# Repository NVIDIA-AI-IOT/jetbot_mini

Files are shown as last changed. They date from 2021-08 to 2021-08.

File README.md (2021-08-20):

# Jetbot Mini

<p align="left">
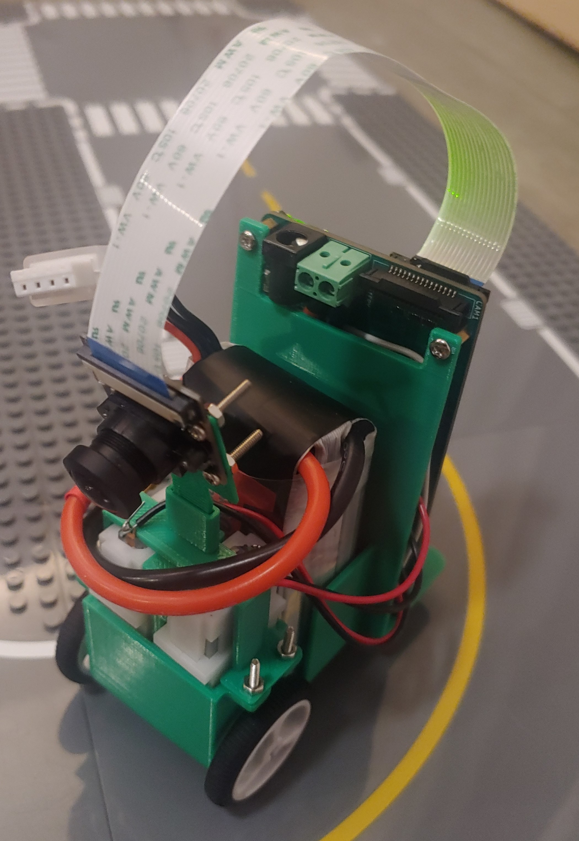
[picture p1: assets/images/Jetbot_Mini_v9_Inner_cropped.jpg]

</p>

This is the Jetbot Mini project, a smaller iteration of the [Jetbot](https://github.com/NVIDIA-AI-IOT/jetbot)! Some key features are as follows:
* Onboard motor controller and battery charger to reduce costs and wire clutter
* Custom baseboard for the Jetson Nano module
* A smaller chassis that can achieve two way traffic (i.e., two robots running on the road at the same time) on the LEGO roads used to test the original Jetbot
* Designed with KiCAD and Onshape for easy maker access

This project aims to be an accessible example project that uses the Jetson Nano platform and a custom baseboard, so any feedback about the design is welcome. 

**Please note that the A00 Baseboard design is not recommended for manufacture, as it requires a rework to work properly and some features have not been fully validated. The A01 Baseboard is currently in development that aims to fix issues found with A00.**

https://user-images.githubusercontent.com/46247601/129587346-760dd624-837d-4d27-9475-d30973f9e246.mp4

## Get Started and Involved!

Refer to [this](https://github.com/NVIDIA-AI-IOT/jetbot_mini/blob/main/docs/getting_started_with_A00.md) document to get a sense of how to use this repository and learn from this project!
This project is intended as a learning tool for makers, and any feedback related to the project is greatly appreciated!
* Report a bug by [creating an issue](https://github.com/NVIDIA-AI-IOT/jetbot_mini/issues)

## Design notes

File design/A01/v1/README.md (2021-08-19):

# Setup

While developing the schematic and layout designs, I used some footprints from SnapEDA; in order to avoid dealing with licensing issues, I will not redistribute those files on this Github and instead link to where you can download the necessary files. 

## Symbol Library Setup

To get setup for the schematic, download the files and import the libraries "Jetbot Mini-rescue" and "Jetbot_Mini_Symbols" in the "libs" folder. 

In order to import a library, go through the following steps:
1. Download the .dcm and .lib files and remember where you stored them on your computer
2. Download the rest of the KiCAD files and open up the .pro file
3. Go to Preferences --> Manage Symbol Libraries --> Project Specific Libraries --> Add Existing Library to Table (folder icon on lower left of dialogue box)
4. Navigate to where the .lib files are stored on your computer and select the files
5. The libraries should be imported and when you try to add a component to the schematic, you should see the libraries show up

You may need the download the following symbol libraries from the KiCAD github: https://github.com/KiCad/kicad-symbols

| Library Name |
| :--- |
| Connector |
| Connector_Generic |
| Logic_LevelTranslator |

## Footprint Library Setup

To get setup for the layout design, you need the following SnapEDA footprint files (you need to make an account if you don't have one already, download the footprint and unzip the package):

| MPN | Device | Reference(s) | Link |
| :--- | :--- | :--- | :--- |
| 692121130100 | USB3 Type A | J8 | https://www.snapeda.com/parts/692121130100/Wurth%20Elektronik/view-part/4900658/?ref=search&t=692121130100 |
| 2309411-5 | DDR4 SODIMM Connector | J1 | https://www.snapeda.com/parts/2309411-5/TE%20Connectivity/view-part/2404627/?ref=search&t=2309411-5 |
| TPD1E05U06DPYR | ESD Diodes | D1, D9 | https://www.snapeda.com/parts/TPD1E05U06DPYR/Texas%20Instruments/view-part/383548/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 |
| BG300-04-A-L-A | Motor Header | J4 | https://www.snapeda.com/parts/BG300-04-A-L-A/Global%20Connector%20Technology/view-part/696206/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 |
| LQH44PN100MP0L | 3V3 Buck Converter Inductor | L1 | https://www.snapeda.com/parts/LQH44PN100MP0L/Murata/view-part/?ref=dk&t=IND_LQH44PN100MP0L&con_ref=None |
| 1935161 | Battery Screw Terminal | J12 | https://www.snapeda.com/parts/1935161/Phoenix%20Contact/view-part/423515/?ref=search&t=1935161 |
| AP6503 | 3V3 Buck Converter | U17 | https://www.snapeda.com/parts/AP6503SP-13/Diodes%20Inc./view-part/562785/?ref=search&t=AP6503 |
| TPD4E05U06DQAR | ESD Diodes | U1, U2, U5, U7, U9, U20, U25, U28 | https://www.snapeda.com/parts/TPD4E05U06DQAR/Texas%20Instruments/view-part/431231/?ref=search&t=TPD4E05U06DQAR |
| 1N4148WT | Diode | D10 | https://www.snapeda.com/parts/1N4148WT/ON%20Semiconductor/view-part/2771069/?ref=search&t=1N4148WT |
| AT24C02D-MAHM-T | EEPROM | U22 | https://www.snapeda.com/parts/AT24C02D-MAHM-T/Microchip/view-part/229652/?ref=search&t=AT24C02D-MAHM-T |
| 74LVC4245A | Level Shifter | U23 | https://www.snapeda.com/parts/74LVC4245APW/Nexperia%20USA/view-part/557968/?ref=search&t=74LVC4245A%20 |
| 74LVC1G126W5-7, 74LVC1G07W5-7 | Tri-State Buffer | U11, U12, U14, U31 | https://www.snapeda.com/parts/74LVC1G126W5-7/Diodes%20Inc./view-part/234182/?ref=search&t=74LVC1G126W5-7 |
| B3SL-1022P | Push Button | SW1 | https://www.snapeda.com/parts/B3SL-1022P/Omron/view-part/215208/?ref=search&t=B3SL-1022P |
| 1-1734248-5 | Camera Connectors | J2, J3 | https://www.snapeda.com/parts/1-1734248-5/TE%20Connectivity/view-part/?ref=te_in&t=1-1734248-5&con_ref=None |
| B340A-13-F | Schottky Diode | D5, D8 | https://www.snapeda.com/parts/B340A-13-F/Diodes%20Inc./view-part/78704/?ref=search&t=B340A-13_F |
| LQH44PN100MP0L | 10uH Inductor for 3V3 Buck | L1 | https://www.snapeda.com/parts/LQH44PN100MP0L/Murata/view-part/4547005/?ref=search&t=LQH44PN100MP |

In order to import the footprints, go through the following steps:
1. Download the KiCAD files to your computer
2. Open the .pro file and click "Footprint Editor" on the top ribbon, the icon is a 6 pin package with green pins
3. Go to File --> New Library --> Create library with name of your choice (should have .pretty extension) in place of your choice, it is typical to keep everything with the KiCAD files --> Choose local
4. Your library should be created, then add the .kicad_mod files from the downloaded SnapEDA folders to the .pretty folder
5. Open up the schematic and go to "Assign PCB footprints to schematic symbols" on the top ribbon, and assign the footprints from your custom library to each of the corresponding symbols

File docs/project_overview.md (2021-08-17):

# Project Overview

<p align="left">

</p>

The [Jetbot](https://github.com/NVIDIA-AI-IOT/jetbot) is a self-driving robot that harnesses neural networks, a camera, motors, and the Jetson Nano module to do cool things like follow roads and avoid obstacles. It is a fantastic learning tool for hobbyists, students and makers to get familiar with neural networks and AI. 

This project, the Jetbot Mini, is meant as a smaller iteration of the [Jetbot](https://github.com/NVIDIA-AI-IOT/jetbot) with a new custom baseboard with an integrated motor controller and battery charger to reduce cost and wire clutter when assembling. The main design goal was to achieve two-way traffic on the LEGO roads used to test the original Jetbot; this goal is meant to facilitate a cool demo and prove how custom baseboards can result in optimizations for these kinds of projects. 

<p align="left">
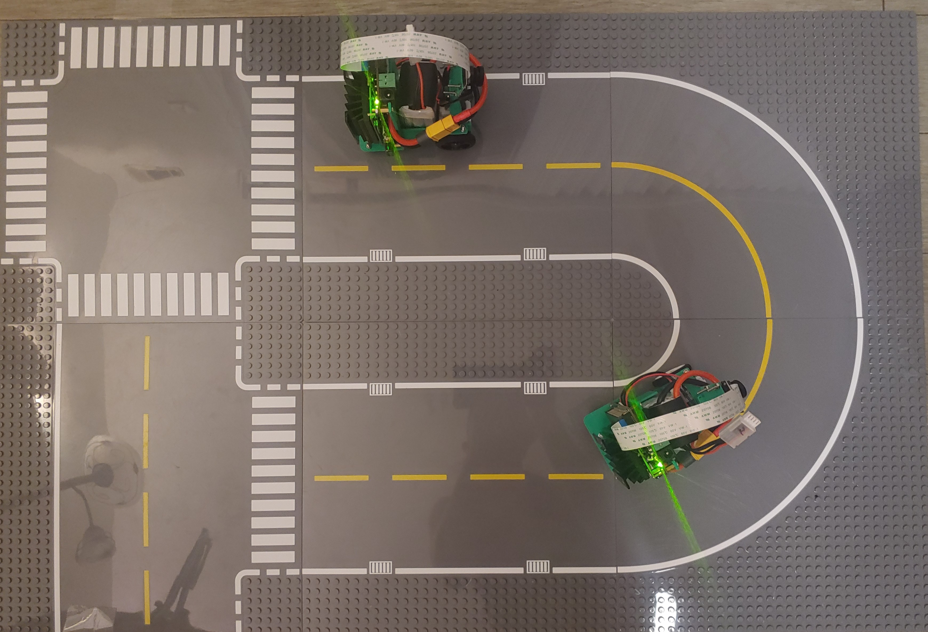
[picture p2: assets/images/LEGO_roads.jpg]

</p>

The overall goal and ethos of this project is to make all the design files open source and provide an example of custom hardware for the Jetson Nano module that makers, students, and hobbyists can learn from and either improve the design, or use it to help them create their own custom hardware. You are encouraged to download the design files and play around with them! 

> As mentioned in the overall README, the A00 baseboard is not recommended for manufacture as the boards have not been fully validated and require an extensive rework to work properly. A01, the next iteration of the schematic, is currently being worked on. 

Another design goal was to make the Jetbot Mini cheaper to manufacture, although that is currently being worked. More information can be found in the bill_of_materials.md file. 

## Feature Set

The following table shows the feature set comparison between the B01 Developer Kit for the Jetson Nano, which was used for the original Jetbot, and the A00 baseboard, used for Jetbot Mini. 

| Features | B01 Developer Kit | A00 Baseboard |
| :--- | :--- | :--- |
| USB | 4x USB 3.0, 1x USB 2.0 Micro-B | 1x USB 3.0, 1x USB 2.0 Micro-B |
| Display | HDMI and DP | None |
| Camera | 2x MIPI CSI-2 DPHY Lanes | 2x MIPI CSI-2 DPHY Lanes |
| Connectivity | Gigabit Ethernet, M.2 Key E | Wifi via USB Dongle |
| Other | GPIO, I2C, I2S, SPI, UART | I2C, UART, Battery Management System, Motor Controller|

Note that a lot of the features from the B01 Dev Kit were cut, and this was done to facilitate a smaller baseboard and thus a smaller overall chassis to hit the two-way LEGO road traffic specification. The following is an IO block diagram showing all the IO on the board:

<p align="left">
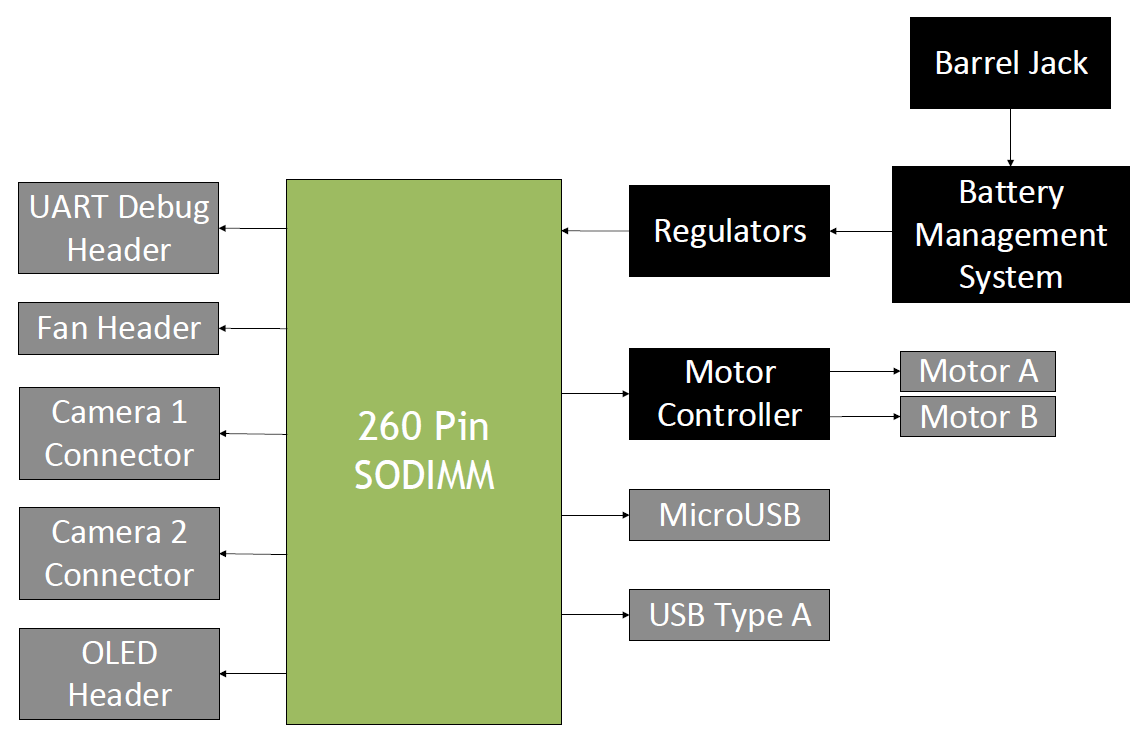
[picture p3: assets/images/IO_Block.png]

</p>

The following table shows what each feature is used for:

| Feature | Justification | 
| :--- | :--- |
| 1x USB 3.0 Type A | Used for Wifi Connectivity to control the robot. Using a wired connection like ethernet is not practical for a moving robot, and eliminating the need for M.2 reduces wire clutter within the robot and cost | 
| 1x USB 2.0 Micro-B | Used for a headless connection to set up the Jetson Nano and for debugging in recovery mode |
| 2x Camera Connectors | Used for vision and movement, and the option for a second camera allows the user flexibility if they want to add an additional camera for more optimized movement |
| OLED Header | Connects over I2C to the Jetson Nano module, and displays the IP address to connect to |
| Fan Header | Four pin connector with tach and PWM used to control an optional fan; note that the Jetbot Mini does not use a fan to reduce chassis footprint | 
| UART Debug Header | Six pin connector compatible with the FTDI friend for debugging and for terminal access | 
| Battery Management System | Eliminates the need for a seprate batter charger and the user does not have to take the Jetbot Mini apart if they wish to charge the battery | 
| Motor Controller | Eliminates the need for a separate motor controller / driver module, which notably the Jetbot requires; this reduces wire clutter and cost |
| EEPROM | Used to store information about the baseboard and used by software; differences in iterations like GPIO might need different software, so this is to help with identification |

A more in-depth dive in to the different features and board design is available in docs/board_design/A00/!

Below shows a comparison between the B01 Dev Kit (Left) and the A00 Baseboard (Right), note how cutting all that IO saved a lot of space!

<p align="left">
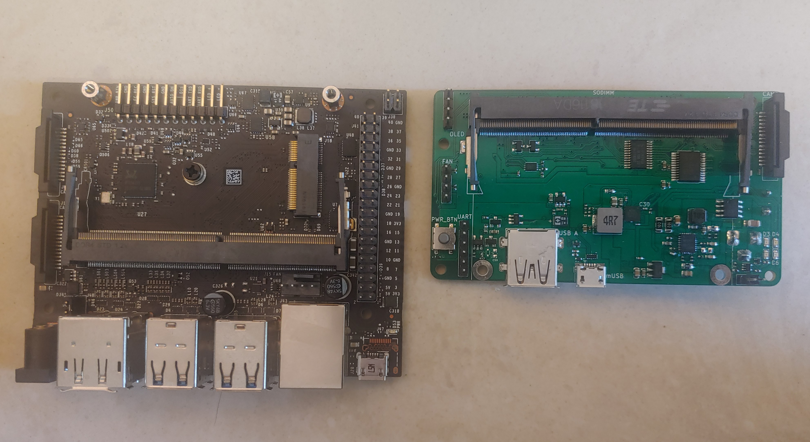
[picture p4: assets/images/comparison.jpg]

</p>

## Design Environment

KiCAD was the tool of choice for schematic and layout design, as it is a free and open-source software widely available for makers. Onshape was used to design the CAD files, and was chosen as it is a cloud-based and easy to use software that is a popular choice among makers. 

## Design Process

The general flow for this project is the following:

Project Conception and Design Goal Specifications --> Schematic + Symbol Design --> BOM Development --> Footprint Design --> Layout --> Design Review --> Gerber Out (means send gerber files to manufacturing house and get design manufactured) --> Bring-Up (Basic power rails and IO check, debug anything not working) and Validate (extensively check each signal, make sure voltage, current and circuit behavior are as expected, check for longevity) Boards --> Chassis Design --> Chassis Prototyping --> Software Integration --> Testing and Acquiring Demo

**And throughout this process, always document every choice thoroughly!!!**

Specifics of the choices for batteries, schematic and layout design, and chassis design are found in their respective folders. 

## Future Work

A01 is still in development but will eventually be gerbered out and validated. In the meantime any Work-In-Progress bugs, features, and edits can be found in the [Issues](https://github.com/NVIDIA-AI-IOT/jetbot_mini/issues) tab of this repository; feel free to create issues, provide feedback and comment on the project!

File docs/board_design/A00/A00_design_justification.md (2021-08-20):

# Design Justification for A00 Schematic and Layout Design

In this document, I will try to explain the justification for every design choice made. First, some basic things:

* I initially chose BOM components from Seeed Studio's libraries, as I thought that I would be getting the boards manufacturing from them. However, during the summer of 2020, the cost of the boards turned out to over a thousand dollars, and we decided to switch to PCBway, who were cheaper and had a more extensive library. 
* Most of the schematic design was referenced from either the B01 Developer Kit (design files can be found [here](https://developer.nvidia.com/embedded/downloads)) or the datasheets of the ICs and components used, and the Jetson Nano datasheet, product design guide, and developer kit user guide were used references extensively (these files can also be found [here](https://developer.nvidia.com/embedded/downloads)).

## Power Tree

After deciding on the initial feature set for the Jetbot Mini, a power tree was drawn up to decide on the power rails and determine the input and output requirements for each rail based on the components on the rails. This data then can be used to choose the buck converter and battery specifications. Data was also taken for the power drawn (in mW) by the Jetson Nano module during various operation modes to factor into the power trees. The [Waveshare Jetbot kit](https://www.waveshare.com/catalog/product/view/id/3756) was used for this testing. The rest of the power consumption data for the different components were referenced from the respective datasheets. Two power trees were drawn up, one with estimated values, and one adjusted for buck converters chosen; the main difference is the efficiency was changed from an assumption to an actual value. The power trees can be found [here](https://github.com/NVIDIA-AI-IOT/jetbot_mini/tree/main/docs/board_design/A00/power_tree).

The power rails are summarized below:

| Power Rail | Power Component Used | Power Component Max Output Current | Max Output Current (from Power Tree) | Components on Power Rail |
| :--- | :--- | :--- | :--- | :--- |
| 5V | GS9238 | 8 A | 4.48 A | Jetson Nano module, motors, OLED, Power Logic, Fan, USB3 Type-A, Motor Driver, Level Shifters |
| 5V_AO | AS78L05 | 100 mA | ~0.0000204 A | Power Logic |
| 3V3 | AP6503 | 3 A | 0.52 A | Cameras, Motor Driver, Level Shifters, Camera Mux |
| 1V8 | TLV70218DBVR | 300 mA | ~0.000049 A | Level Shifters |

## Battery Choice

The battery needed to be small, inexpensive, and be able to ideally power the Jetbot Mini for 1 hour. After creating the power tree, typical current draw from the battery was determined to be around 1.235 A at 12 V, and so a 1500 mAh battery was pursued. The most viable and readily available option was an RC LiPo battery; note that the eventual battery charger chosen is technically a Li-Ion battery charger, but the two battery chemistries have a similar charging curve and I received approval to use it for LiPo batteries. The following table shows some of the options considered at the time:

| Battery Name / Manufacturer | Battery Type | Capacity | C Rating | Size (L x W x H, in) | Connector Type | Price Per Battery | Comments | Links |
| :--- | :--- | :--- | :--- | :--- | :--- | :--- | :--- | :--- |
| INIU Power Bank | 5V / 3A High-Speed 2 USB ports | 10000 mAh | N/A | 5.1 x 2.7 x 0.6 | USB | $19.99 | Used on Original Jetbot | [Amazon](https://www.amazon.com/gp/product/B07H6LB4J4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) |
| Tattu | 3S LiPo | 1300 mAh | 45 C | 2.83 x 1.44 x 0.89 | XT60 | $15.99 | Cheap and small, but low capacity | [Amazon](https://www.amazon.com/Tattu-Battery-1300mAh-11-1V-Airplane/dp/B013I9RLVK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) |
| HOOVO | 3S LiPo | 1500 mAh | 120 C | 2.68 x 1.36 x 1.08 | XT60 | $15.50 | High discharge rate! 2 Pack. | [Amazon](https://www.amazon.com/HOOVO-Quadcopter-Helicopter-Airplane-Multi-Motor/dp/B07W1PFWB6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) |
| GOLDBAT | 3S LiPo| 1500 mAh | 100 C | 2.83 x 1.38 x 1 | XT60 | $13.99 | 2 Pack. High discharge rate, relatively low capacity. | [Amazon](https://www.amazon.com/GOLDBAT-Softcase-m4-fpv250-Shredder-Helicopter/dp/B07ZFDJWR1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) |
| Youme Power | 2S LiPo | 5200 mAh | 50 C | 5.31 x 1.65 x 0.83 | Deans T Plug | $17.99 | 2 Pack. Seems to be a bit large for a 2S battery | [Amazon](https://www.amazon.com/Battery-5200mAh-Helicopter-Airplane-Racing/dp/B07LGSCPFG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) | 
| Ovonic | 2S LiPo | 5200 mAh | 50 C | 5.39 x 1.81 x 0.94 | Deans T Plug | $15.50 | 2 Pack. | [Amazon](https://www.amazon.com/OVONIC-Batteries-Dean-Style-Connector-Associated/dp/B07CVBQW5T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) |  
| Tattu | 2S LiPo | 450 mAh | 75 C | 2.40 x 0.63 x 0.59 | XT30 Plug | $8.46 | 4 pack. Smallest battery so far! But also smallest capacity. | [Amazon](https://www.amazon.com/Tattu-Packs-450mAh-7-4V-Battery/dp/B07K18DJG5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) |

I decided to go with the GOLDBAT because it was the smallest and cheapest battery available while hitting the hour long specification. 

Some additional notes about batteries and battery chargers:
* The C-rate specifies the speed a battery is charged or discharged. For example, a 1000 mAh battery discharged at 1 C should be able to maintain 1 A for 1 hour, and if it is discharged at 2 C, it should maintain 2A for 30 minutes. RC batteries in particular need to deliver huge amounts of current, and thus have high C ratings; however, this feature is not necessary for this project. 
* NTC (negative temperature coefficient): resistance of the material decreases with temperature.
* Constant Current: Vary the voltage to maintain a constant current flow, switching off when the voltage reaches the level of a full charge. The design is usually used for NiCd and NiMH cells or batteries
* Constant Voltage: "allows the full current of the charger to flow into the battery until the power supply reaches its pre-set voltage.  The current will then taper down to a minimum value once that voltage level is reached."

References: https://www.heliosps.com/knowledgebase/battery-charging-methods-terminology/ and Battery University. 

## Schematic Design

In general:
* 0 ohm resistors are used throughout the design for testing purposes; they can be used as points to attach probe wires and inject noise.
* You will often see capacitors on the input rails to ICs and power supplies; these capacitors are there to help deal with noise, stabilize the power supply and voltage ripple, and help with sudden current requirements. The impedance of a capacitor is dictated by 1/jwC, where w is 2 x pi x frequency and C is the capacitance; at high frequencies, the impedance of a capacitor is near zero, which means the component is essentially a short to ground. This means high frequency noise is shunted to ground instead of entering the IC. Also, the capacitors act as small voltage reservoirs, and thus if the input voltage dips below the stored voltage, the capacitor can briefly supply power to the IC. In addition, the smaller 0.1uF capacitors are to help if the IC needs to pull a sharp current suddenly, perhaps due to a change in load. Larger capacitors will have ESR (equivalent series resistance) and ESL (equivalent series inductance) which will fight against that current pull, but smaller capacitors have smaller parasitics that help facilitate large current draw. These small 0.1uF capacitors do not store that much power, but will help with the sudden rising and falling edges for things like digital circuits. 
* The following [forum page](https://forum.digikey.com/t/calculating-capacitor-esr-from-tan/2633) is useful for calculating MLCC parasitic values. MLCC ESR and ESL values are also often listed on the manufacturer website in the form of graphs.

### Page 2 of A00 Schematic: Camera

<p align="left">
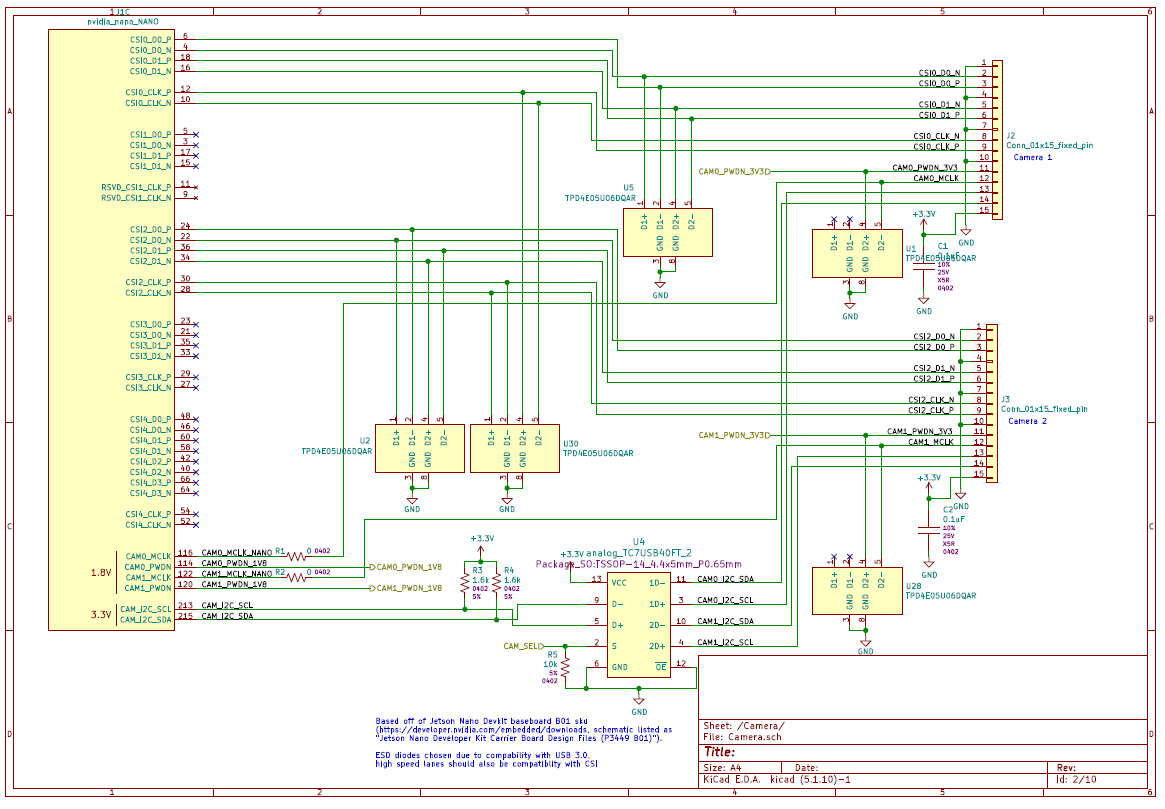
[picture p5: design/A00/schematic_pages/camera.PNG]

</p>

* Most of the camera connector (J2 and J3) connections were referenced from the B01 Developer Kit files. 
* No ESD on the CAM0_I2C_SDA, CAM0_I2C_SCL, CAM1_I2C_SDA, and CAM1_I2C_SCL lanes, as the TC7USB40FT has ESD on the output lines.
* TPD4E05U06DQAR ESD diodes chosen due to availability in target manufacturer libraries and because they are compatible with USB 3.0; using these diodes for the CSI lanes eliminates the need for separate ESD diodes. They have 0.5pF capacitance. Datasheet states compatibility with high speed signals. 
* CAM0 and CAM1 PWDN signals are level shifted from 1V8 to 3V3 for compatibility with new higher quality raspberry pi cameras; note that the B01 Developer Kit is not compatible with these cameras. 
* U4 is a mux used to switch between camera 1 and camera 2. 
* Note that when the Jetson Nano module boots up, it pings the camera I2C lanes to see if a camera module is attached and employs a startup sequence with PWDN; if no camera module is detected, calling camera commands will not send any data to the camera lanes. 
* Note that only a 0.1 uF capacitor is needed on the power rail of the camera connector, as the parasitics from the ribbon cable that connects the camera module to the camera connector prevents the camera board from seeing the additional capacitors effectively. The current spikes that the capacitors are meant to deal with are negated by the inductance of the camera ribbon cable.
* R5 is a pull-down resistor for the camera select pin of the mux, so that the default setting for the mux is lane 1. 

### Page 3 of A00 Schematic: Motors

<p align="left">
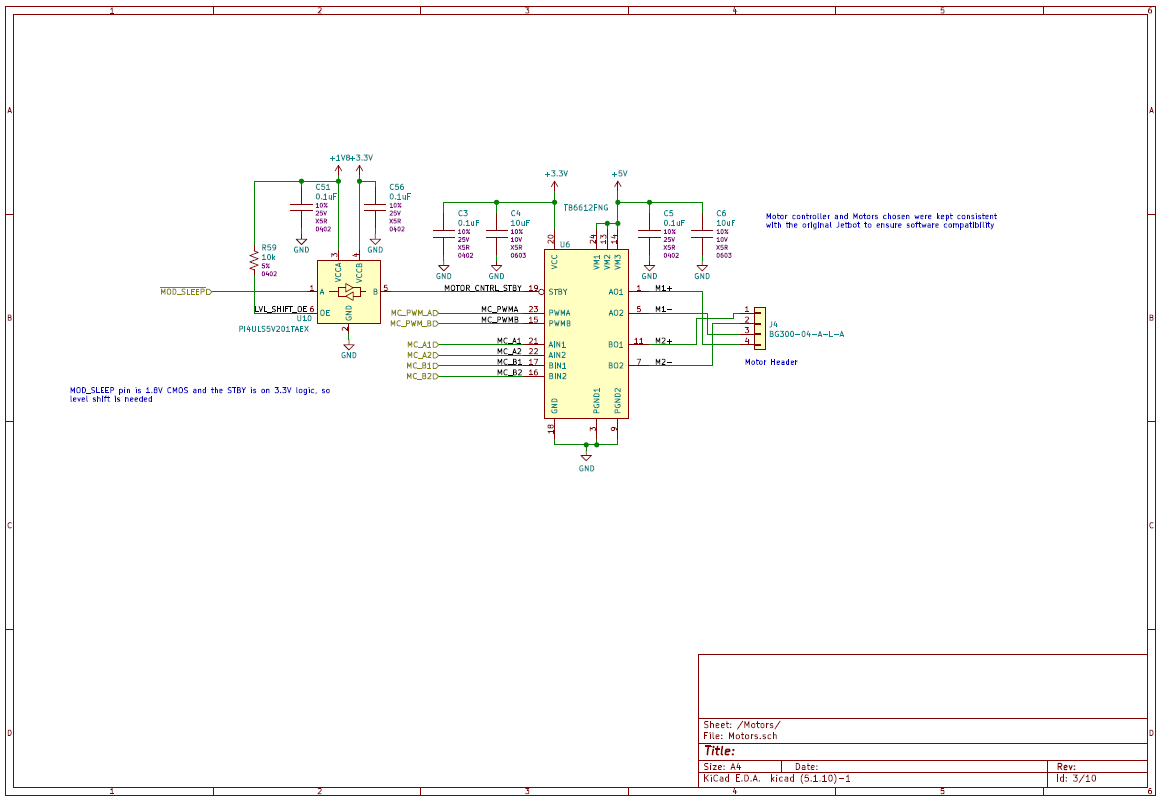
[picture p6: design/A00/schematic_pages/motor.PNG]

</p>

* The same motor controller IC as the Jetbot, the TB6612FNG, was used to ensure compatibility with Jetbot software. Note that the A00 baseboard uses GPIO instead of I2C to control the motors.
* Motor speed is controlled via PWMA and PWMB. 
* Motor A direction is controlled by AIN1 and AIN2, and motor B direction is controlled by BIN1 and BIN2. If both pins are off or on, the motor is turned off. See TB6612FNG datasheet or tutorial for exact directions based on pins. 
* Capacitor values on power rails were suggested by datasheets, and voltage ratings are high because those capacitor values are used elsewhere on higher voltage lines; using the same capacitor saves cost by eliminating the need for a unique part on the BOM. 
* The MOD_SLEEP pin that controls standby for the motor controller (i.e., tells the motor controller to turn off for a bit and conserve power) is on 1V8 logic, and the STBY pin is on 3V3 logic, so the level shifter is needed to translate between the two voltage levels. 
* Motor header is surface mount and placed underneath the board, as initially I thought that the chassis design would put the motors underneath the board, and so it would be easier to connect if the headers were on the bottom of the board. The Jetbot Mini test chassis ended up mounting the baseboard vertically, but it still worked out OK as the motors were in front of the motor headers.
* Note that different motors were used than the Jetbot to facilitate a smaller chassis design; the motors chosen ended up having a lower stall current than the TT motors used for the Jetbot, and thus would mean less strain on the 5V Buck Converter. 
* R59 pulls output enable high to enable the level shifter.

### Page 4 of A00 Schematic: USB

<p align="left">
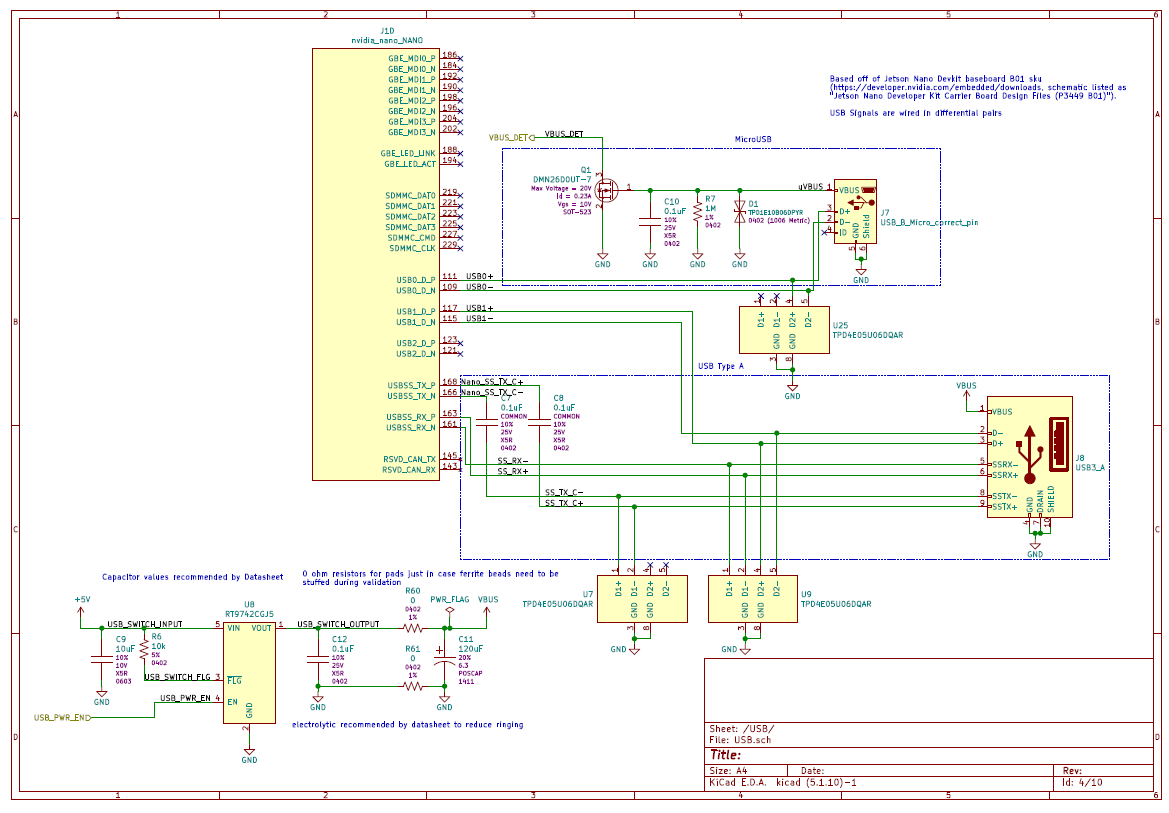
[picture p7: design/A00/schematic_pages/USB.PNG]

</p>

* This part of the circuit was heavily referenced from the B01 Developer Kit schematic.
* TPD4E05U06DQAR ESD diodes were chosen due to their compatibility  with USB devices and should be placed as close as possible to the connector on the layout.
* microUSB: J7
  * D1 to protect against ESD strikes when user pulls microUSB head in and out of the connector. 
  * R7 pulls the gate of Q1 initially low, and when a microUSB is connected VBUS_DET is connected to ground and lets the Nano module know that something is connected.
* USB3 Type-A: J8
  * C7 and C8 are AC-coupling capacitors and should be placed as close as possible to the transmission source on the layout. AC-coupling capacitors block DC bias. 
  * The USB switch U8 is needed to protect the host, as the USB might be drawing too much current, and also allows for power cycling the USB. The chosen part hits the required spec of max current draw for USB3 Type-A being 0.9 A. 
  * Capacitor values chosen based off the datasheet. 0 ohm resistors there just in case ferrite beads need to be stuffed during validation or if found that they are necessary.
  * C11 was switched from electrolytic to POSCAP to reduce the footprint size. 

### Page 5 of A00 Schematic: Fan

<p align="left">
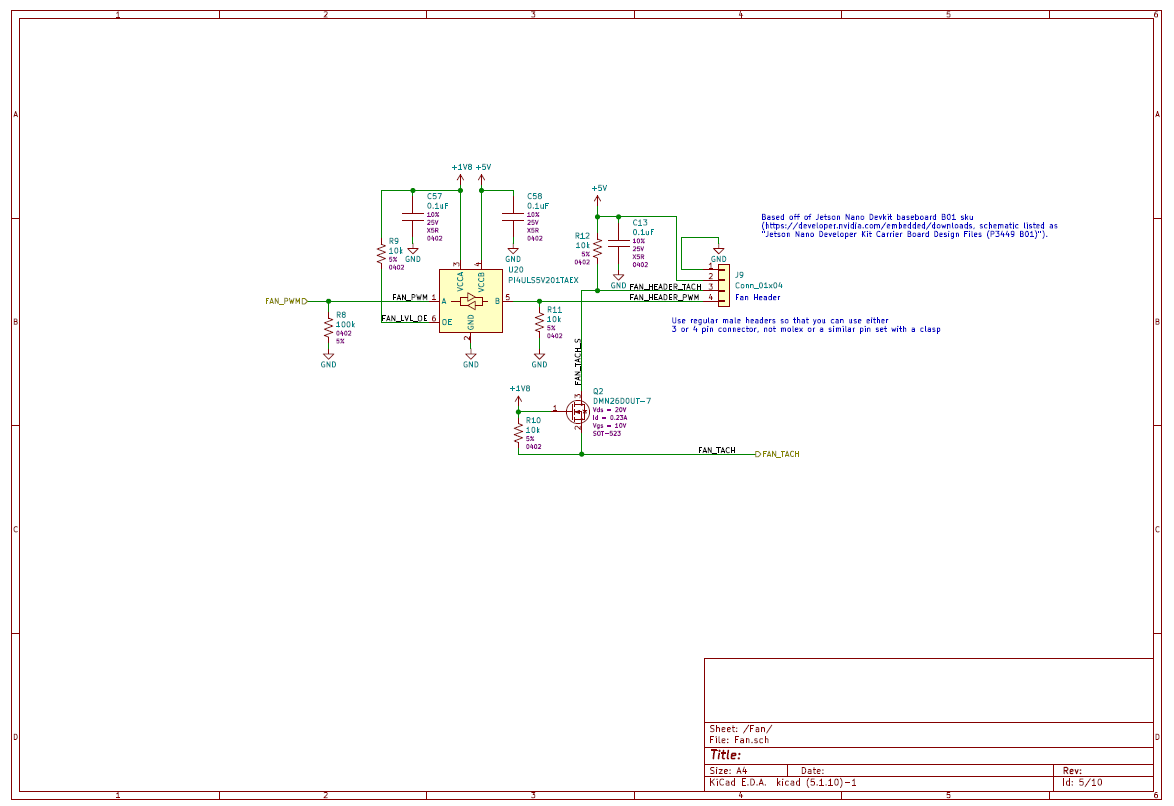
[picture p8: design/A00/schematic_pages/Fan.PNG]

</p>

* PWM level shifted to 5V to work properly with fan. 
* C13 is a decoupling capacitor for power rail of the fan. 
* PWM signals pulled low via R8 and R11, so initial state of PWM is zero.
* The Tach signal uses a level shifter (that should only be used with open drain signals!) that works as follows: the FAN_HEADER_TACH signal will output a square wave that drives low and has an open drain high that is pulled to 5V via R12. When the signal is driven low, the drain of Q3 is drive low. Before this time, Q2 was off as the gate and source are connected to 1V8, meaning Vgs = 0 < Vgsth; however, when the drain of Q2 is driven low, the body diode is in forward bias and thus connects source to zero. The current path from 1V8 to 0 has R10 in the way, so current is not too high. Q2 is turned on, and the FAN_TACH sees a logic low. When FAN_HEADER_TACH is driven high to 5V, the body diode is in reverse bias, which disconnects the source from the drain and turns off Q2. In this state, FAN_TACH sees 1V8, or a logic high. Thus, FAN_TACH sees a square wave ranging from 0 to 1V8, whose frequency is proportional to the fan speed. 

### Page 6 of A00 Schematic: Power_1

<p align="left">
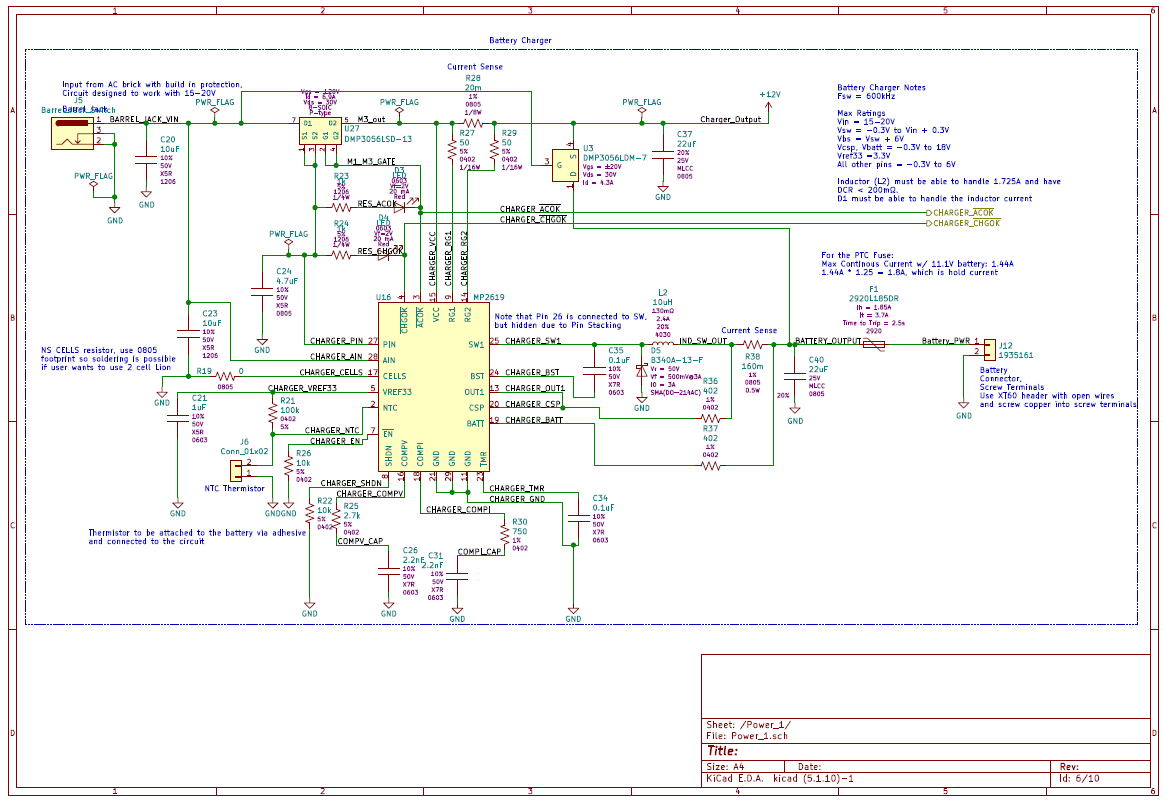
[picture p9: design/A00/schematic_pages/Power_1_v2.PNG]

</p>

* This is the battery charger circuit, with the battery charger IC of choice being MP2619 due to its low cost, availability and my team's experience with it. 
* Most of this circuit was referenced from the MP2619 datasheet example circuit. 
* Some noteworthy features / things to keep in mind:
 * This charger circuit DOES NOT feature charge balancing, so this will effect the longevity of your batteries. 
 * An NTC thermistor is required for charging to occur. If the thermistor becomes too hot or cold, charging will stop. 
 * DMP3056LSD-13 and DMP3056LDM-7 chosen with Vds that can handle at least 30V, as the highest voltage the battery charger can take is 26V. 
 * R23 and R24 values calculated by: (20 V - 2 V) / 1000 = 0.018 A, with LEDs chosen to light up bright around 20mA. However, these resistor values were too low as 18mA is cutting it too close to max current of 20mA that is typical for LEDs, and were changed in A01. 
 * R19 is no-stuffed (component not assembled) in order to give the user the option to 2S batteries. Currently with it floating the charger is configured for charging 3S batteries.
 * R21 is 100k in order to align with the 100k NTC thermistors purchased, as they were the only ones I could find decently priced with the headers I wanted at the time. 
 * J12 is the screw terminal to connect the battery; the battery I chose has an XT60 header, so the plan was to purchase an XT60 female header to wire adapter and screw the wires into the header. The XT60 headers are supposed to be 12 awg. Note that when I tested them with the A00 baseboard, the screw terminals were too small to fit the XT60 connectors, and I needed to trim the wires to fit. 
 * F1 chosen based off of power tree calculations: typical current draw is about 1.235A, and given 25% margin: 1.235 * 1.25 = 1.54 A, and fuse chosen with trip around 1.85A. 

### Page 7 of A00 Schematic: Nano_IO

<p align="left">
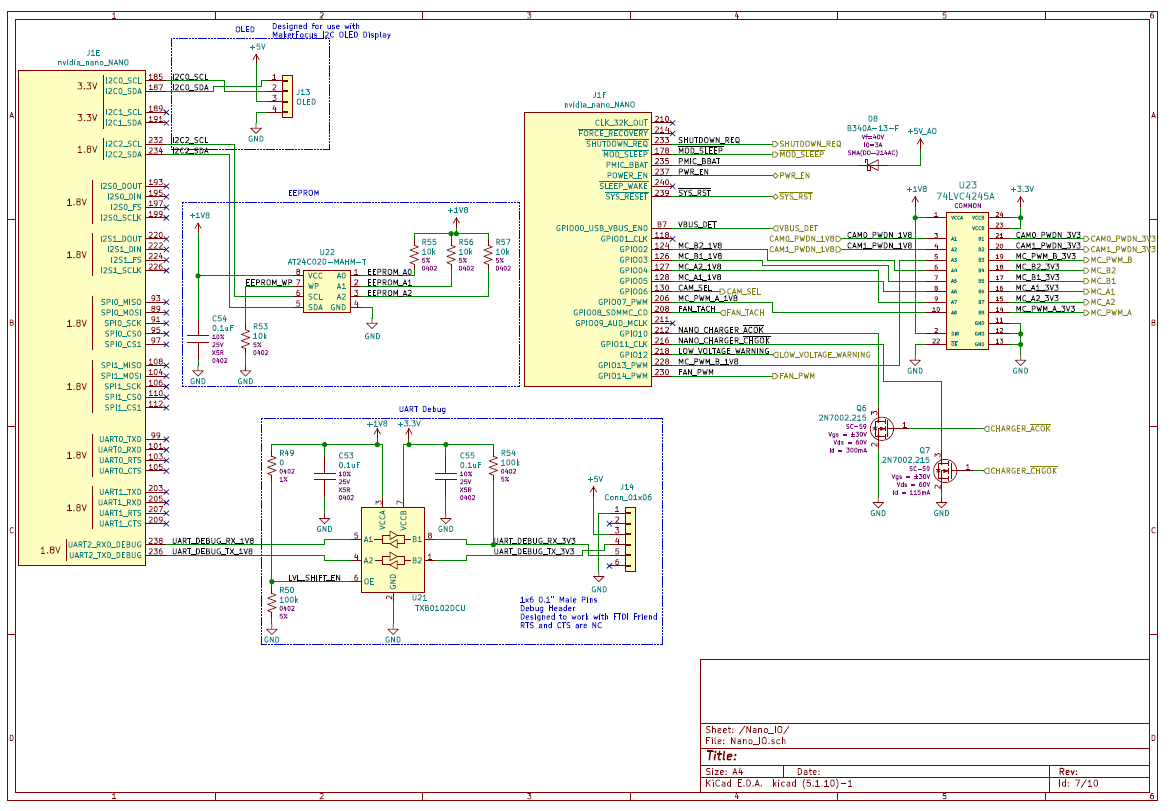
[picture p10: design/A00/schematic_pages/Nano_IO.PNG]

</p>

* Note that the I2C Lanes for the OLED display were connected incorrectly; the Jetbot uses I2C1 not I2C0, and thus the OLED display was not lighting up properly. This was fixed in A01. 
 * Jetbot uses pins 3 and 5 on the GPIO 40 pin expansion header, which correspond to I2C1 lanes. 
 * I2C OLED Display meant to go over the SODIMM module
* U22: EEPROM used for Jetson Nano module, and is the same part as the one on the B01 Dev Kit. 10k resistors used as pull-up. Note that MLCC C54 is rated for 25V because there are other places that require 0.1uF with higher voltage ratings, and using the same capacitor as long as the voltage rating is above the requirement is advantageous to reduce the number of unique parts the manufacturer has to assemble. R53 used as a pull-down resistor.
 * EEPROM is to store information about the baseboard, for example if remoting into the board you can check the EEPROM and determine information about the board. For example, A00 vs A01 iteration might have differences that software needs to know about, like GPIO definitions, etc.
 * Write Protect: Connecting the WP pin to GND will ensure normal write operations. When the WP pin is connected to VCC, all write operations to the memory are inhibited.
* UART Debug
 * 6 pin connector used to maintain compatibility with [FTDI friend adaptor](https://www.adafruit.com/product/284).
  * Note that the RX and TX are routed incorrectly, and needed to be switched with A01. 
 * FTDI friend requires 3V3 – 5V signal lines, and tegra GPIO are on 1V8 logic, so need level shifter. 
  * TXB0102DCUR replaced TXB0302DQMR, as the latter was not available in Seeed’s or JLCPCB’s libraries.
* PMIC_BBAT powered from 5V_AO instead of a coin cell battery or supercap, as 5V_AO was already available and required less space on the PCB.
 * PMIC used to maintain RTC (real-time clock) voltage when VDD_IN is not present.
 * Requires further investigation, as 5V_AO is only on when VDD is present. 
* MOD_SLEEP connected to the standby pin on motor controller for power saving purposes.
 * Pin is low when module is sleeping, and high when module is in normal operation. Using this pin to control standby means the motor controller is on standby and using less power when module is sleeping.
 * For Motor controller STBY Pin: VIH (STB) = VCC x 0.7 – VCC+0.2 and VIL (STB) = -0.2V – VCC x 0.3, with VCC = 3.3V, thus need level shifter
* PWR_EN is fed from the 5V buck PGOOD, thus module will turn on when 5V rail is ready. 
 * PGOOD signal is actively held low during shut down and soft-start status, open drain during soft start, and pulled up via external resistor to 5V_AO when soft start is finished. PWR_EN pin is on CMOS 5V logic.
* SHUTDOWN_REQ is fed to the power logic to turn the Nano module off. 
 * Note that there was a big issue with the power logic for shutdown request, as it holds the RESET pin of the SR latch low, preventing the power logic from turning on the 5V buck converter
* SYS_RST used to turn on USB power switch and 3V3 buck, after the module turns on after receiving PGOOD signal.
 * Note that SYS_RST is on 1V8 logic, while the 3V3 buck converter enable signal requires V_IH = 2.5V, so the 3V3 buck converter was not turning on at startup. This is addressed in A01.
* VBUS_DET used to detect the presence of microUSB in the connector via a MOSFET level shifter. 
 * Note that power is supplied by the MicroUSB host. 
* GPIO10 on pin 212 and GPIO11_CLK on pin 216 used to detect charger ok and AC ok from the battery charger, they were available for use and thus thought it was a good idea to have additional information going to the module. The pins will be pulled low when ACOK and CHGOK go high. Internal pullups on the pins means default state will be logic high.
 * Note that if LED is ON, then corresponding pin is LOW, which means GPIO should read HIGH. ACOK and CHGOK are active low pins. 
* Low voltage warning from comparator circuit explained in the schematic, fed to the module for additional information. Purposely used open drain buffer to be on 1V8 logic. 
* Motor controller and CAM PWDN pins fed through a level shifter to match the requirements of the TB6612FNG and camera.
 * The GPIO are connected the way they are to ensure easy access on layout. 
* Q9 and Q10 chosen as they were parts used elsewhere. 
* Q6 and Q7 parts needed a large Vgs tolerance as the gate was exposed directly to voltage from the barrel jack.
* D8 (B340A-13-F) chosen for similar specs with equivalent on B01 Dev Kit Schematic: D64 (LS34SG).
* For U21, B01 uses TXB0302DQMR, we used TXB0102DCU, at the time was searching through Seeed’s parts library and come up with level shifter with similar specs.

### Page 8 of A00 Schematic: Power_3

<p align="left">
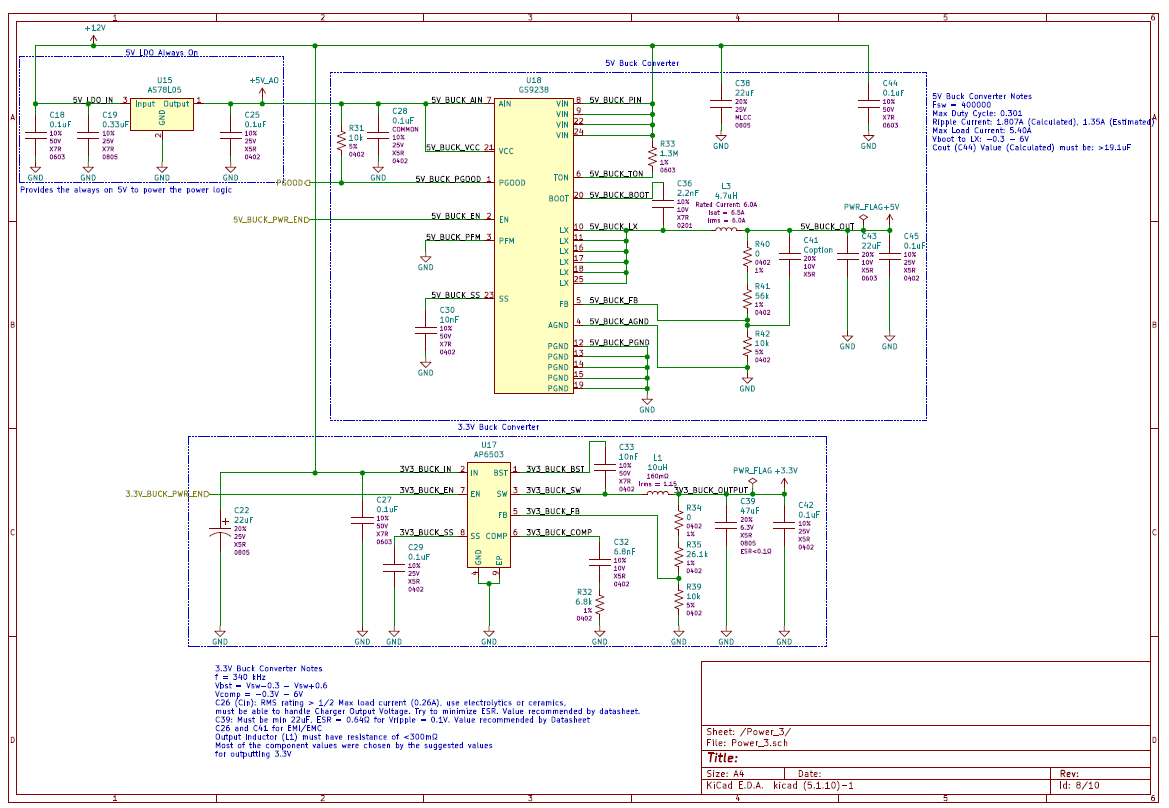
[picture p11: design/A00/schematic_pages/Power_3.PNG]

</p>

**Please note that the buck converter calculations for the 5V and 3V3 bucks were incorrect, and are currently being fixed for A01.**

* Calculate MLCC ESR and ESL by looking on charts given from manufacturer website at the target frequency for the buck converter. 

### Page 9 of A00 Schematic: Power_2

<p align="left">
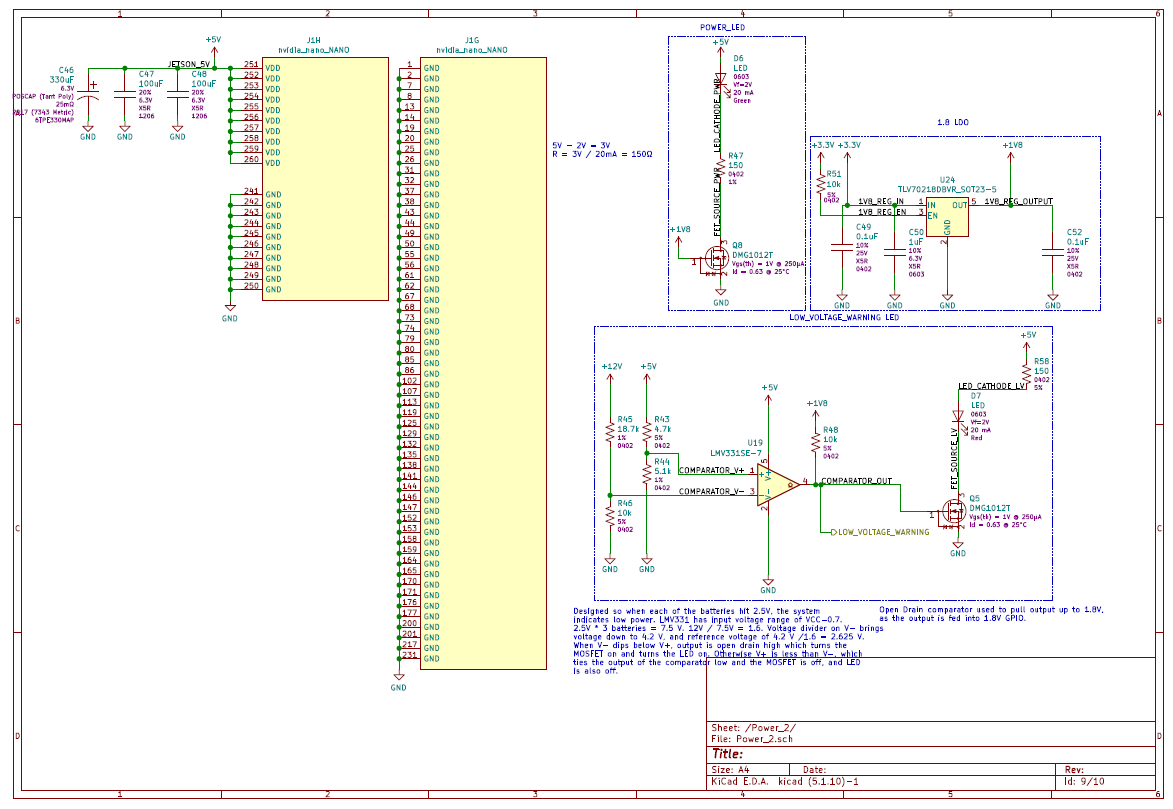
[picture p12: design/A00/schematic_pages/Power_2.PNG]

</p>

**Please note that the low battery LED comparator's threshold is way too low. To properly understand state of charge vs voltage, use the following [link](https://blog.ampow.com/lipo-voltage-chart/)

* C46 switched from electrolytic to POSCAP to save on footprint size.

### Page 10 of A00 Schematic: Power Logic

<p align="left">
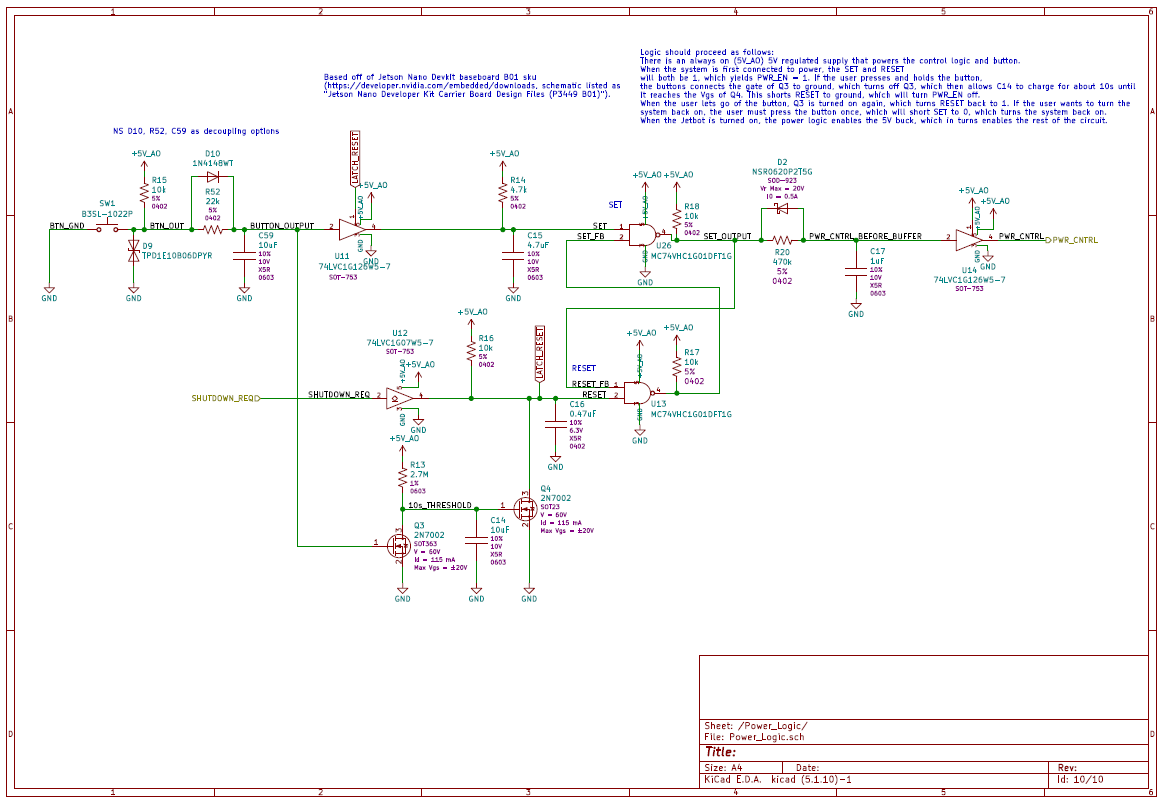
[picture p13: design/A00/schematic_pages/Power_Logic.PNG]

</p>

* D10, R52, and C59 are no-stuffed debugging options. However, R52 needed to be stuffed to connect the button to the rest of the circuit. 
* ESD diode D9 used to protect the rest of the circuit from ESD strikes on button. 
* Logic explained in schematic.
* "Disable for auto power on” jumper is always connected, so default state when powered on should be off.  

## Summary of Issues with A00 Schematic Design Identified During Bring-Up and Design Reviews

| Sheet | Issue | Solution in A01 |
| :--- | :--- | :--- |
| Power_Logic, Power_1 | R52 and R22 were not stuffed | BOM makes sure R22 and R52 are stuffed |
| Power_Logic | SHUTDOWN_REQ is holding RESET or SR Latch low, preventing the 5V rail of the baseboard from turning on | Add a tri-state buffer in between SHUTDOWN_REQ and U12 buffer |
| Nano_IO | RX and TX are not routed to match FTDI Friend | Swap RX and TX in schematic and layout for UART Header |
| Nano_IO | No FORCE_RECOVERY option | Added two pin header for FORCE_RECOVERY option |
| Power_1 | XT60 connectors need to be trimmed to fit Screw terminal | Need to consider different Screw Terminals or connector |
| Power_3 | 3V3 Buck converter never turns on as SYS_RST is too low voltage for enable pin | Added transistor level shifter in between SYS_RST and 3V3 Buck Converter enable |
| Nano_IO | OLED display does not turn on as I2C is routed to I2C0 instead of I2C1 | Change I2C to go to I2C1 for schematic and layout |
| Power_3 | 5V Buck Converter boots up to around 5.20 - 5.38 V | Fixed feedback network, but also need to consider different buck converter |
| Power_2 | Low Power LED Flickers and Voltage threshold is too low | Added hysteresis and fixed voltage levels |

## Layout Design

After schematic design was completed, a BOM was formulated and the footprints for the chosen parts were loaded into KiCAD. Some footprints were made by me, and others I downloaded from SnapEDA. The list of footprints that I downloaded from SnapEDA can be found [here](https://github.com/NVIDIA-AI-IOT/jetbot_mini/blob/main/design/A01/v1/README.md).

The main design process for PCB layout is as follows:

Import Netlist --> Place IO and Footprints --> Determine Board Cutout --> Route High Speed Signals --> Route Power Paths --> Route Everything else --> Run DRC

<p align="left">
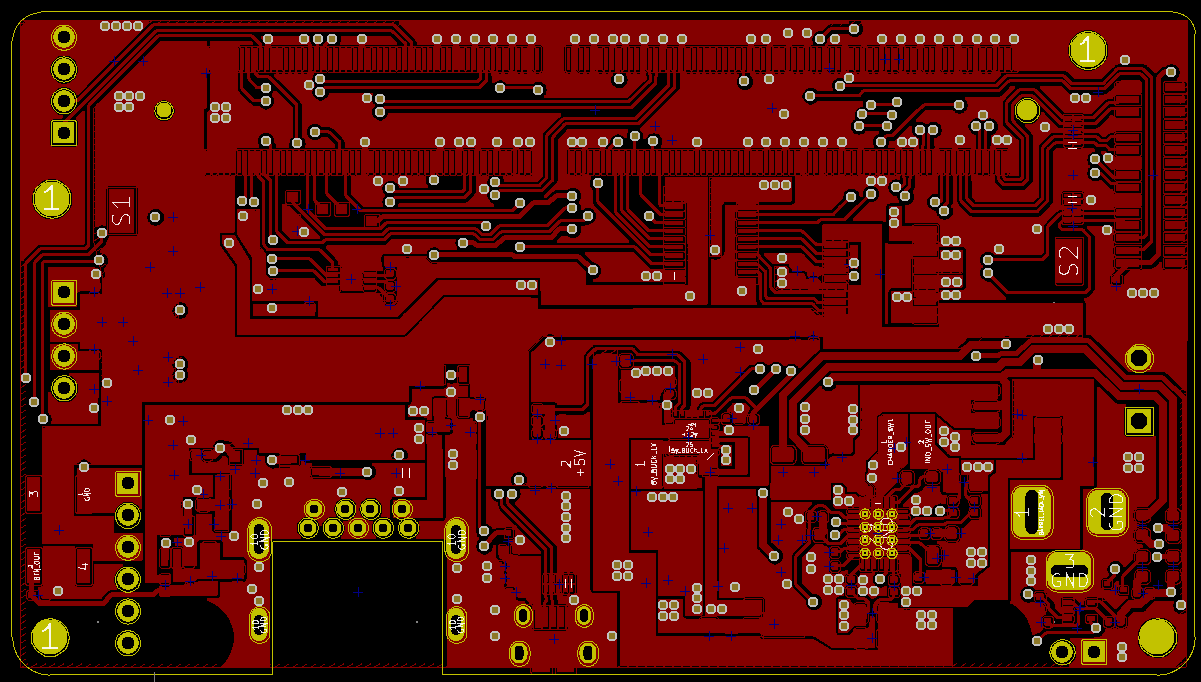
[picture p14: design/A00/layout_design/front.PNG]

</p>

<p align="left">
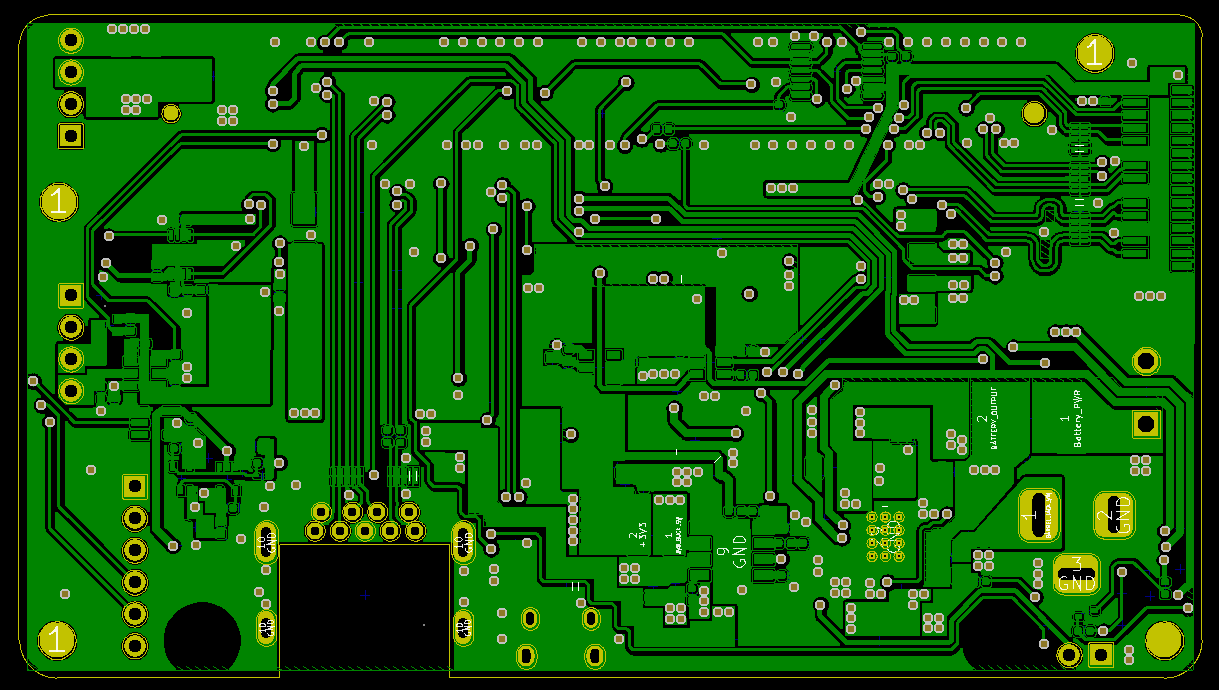
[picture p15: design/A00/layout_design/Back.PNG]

</p>

### General Notes

* The stackup for this board is four layers: signal, gnd, gnd, signal. The inner two ground layers are used as reference layers for diff pairs on the top and bottom layers and for shielding from switching node noise from buck converters. 
* Copper pours were used wherever possible in order to minimize the resistance of the paths that the current travels through. Having a thin section of the power path essentially creates a resistor at that point. 
* A good rule of thumb for determining how many vias you need for current paths is 1 A / via. 
* A good mindset to have when starting routing on two layers is to have all the traces on one side be horizontal or vertical, and the traces on the other side be the opposite. This way the traces mesh together well when vias are used.
* I tried to place components as close as possible to the needed pads on the SODIMM. 
* Note that headers should be placed multiples of the pin pitch away from each other so that continuous rows of headers can be used. For example, the pitch used for this project is 2.54 mm, and so J9 is placed at x = 98.87, and J14 is placed at 103.95 mm, so 103.95-98.87 = 5.08, which is divisible by 2.54 mm.
* I used the Saturn PCB and KiCAD trace tool to calculate impedance for traces and determine necessary trace widths to meet high speed signal requirements. These signal requirements can be found in the Jetson Nano datasheet. 
* I referred to example layouts on datasheets whenever applicable. 
* The reference ground planes underneath the ESD and SODIMM high speed connections must be voided to avoid parasitic capacitance. Note that when the differential pairs pass through the ESD diode or come out of the SODIMM, the traces are not able to maintain proper impedance matching properties.
 * Ensure that there is a voided area that is 0.2 mm larger on all sides underneath the high speed pads on the SODIMM and through the ESD.
* GS9238 (5V Buck Converter)
 * The current return path was kept as small as possible. 
 * There are less vias near pin 4 ground, as it is the analog ground and is used for control logic. Pins 12, 13, 14, 15, and 19 are used for Power ground, and thus require the 1A/via rule of thumb.
* Silkscreen was used to mark important IO. 
* Use Zone priority levels to create copper pours!
* MP2619
 * Current sense resistor R38, and resistors R36 and R37 are shown below, and must be routed like the following image in order to have most of the current pass through the current sense resistor and R36 and R37 get accurate data readings to provide to the battery charger.

<p align="left">
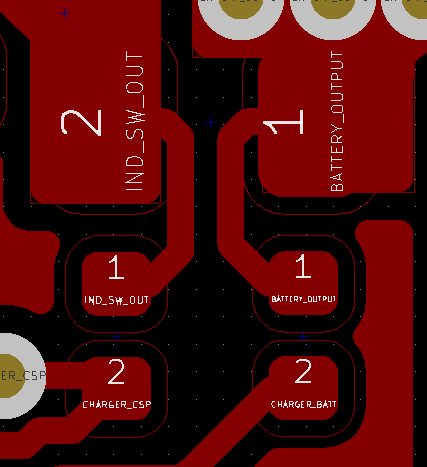
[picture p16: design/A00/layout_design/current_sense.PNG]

</p>

### Component Placement

<p align="left">
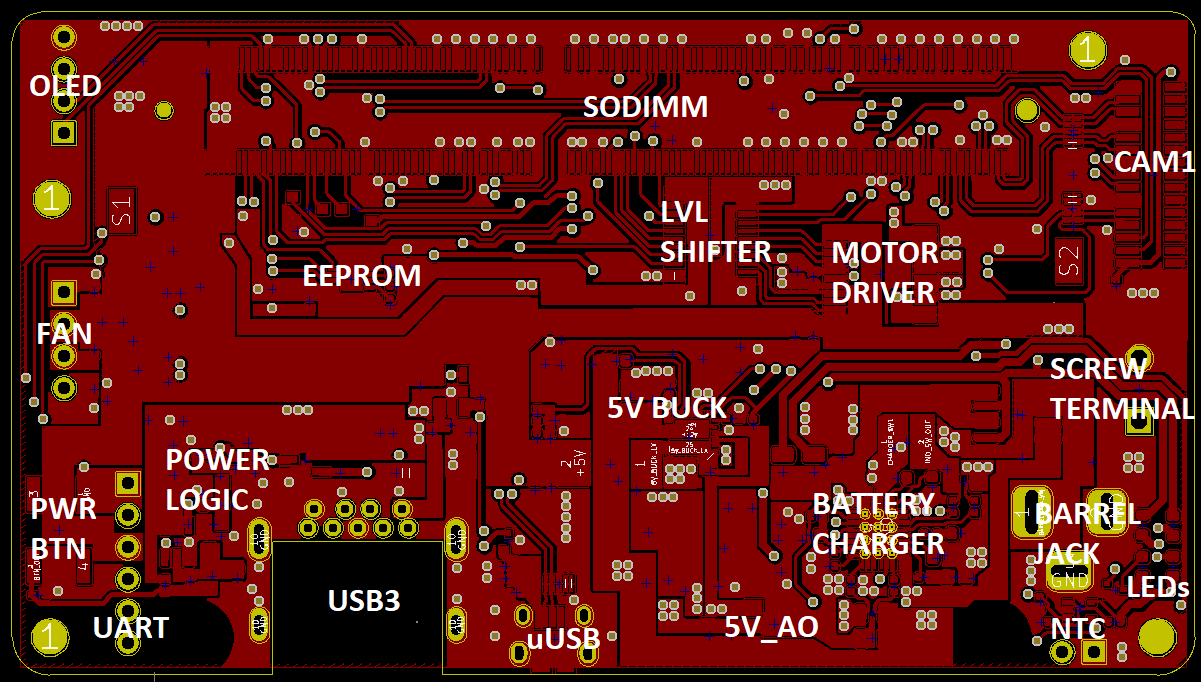
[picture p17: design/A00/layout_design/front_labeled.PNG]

</p>

<p align="left">
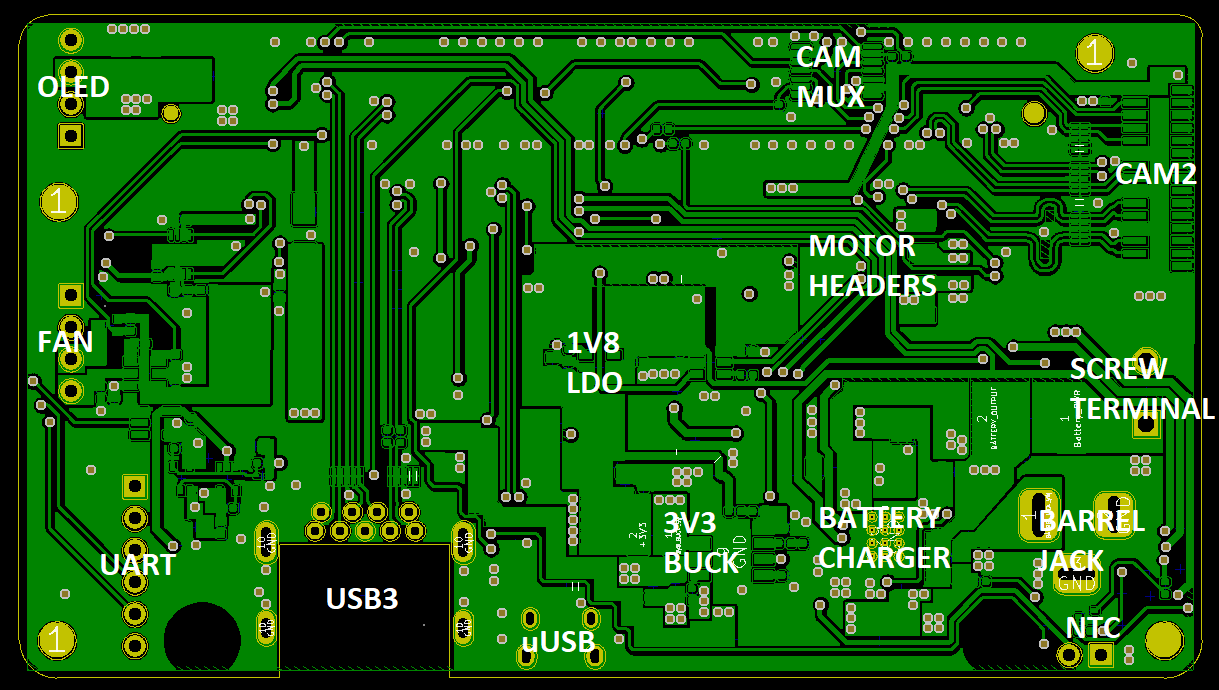
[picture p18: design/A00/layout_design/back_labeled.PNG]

</p>

* USB3 and uUSB were placed underneath the Jetson Nano module to save space; there is approximately 5mm of space between the baseboard and the Jetson Nano module, so a mid mount USB was used to make it fit. 
* The battery charger was placed as close as possible to barrel jack and screw terminal.
* The 5V Buck, 3V3 Buck and 5V_AO regulator were placed as close as possible to the battery charger, and the power branches out to the rest of the board. 
* Screw terminals face inward as I initially thought the chassis design would have the battery underneath the baseboard, so having the terminals face inward would allow for easier connection. 
* Power logic was placed as close as possible to the power button.
* The motor headers are on the bottom of the baseboard as I initially thought the chassis design would have the motors underneath the baseboard, so this placement would allow for easier connection. 
* A way to improve on this design might be to move the headers underneath the Jetson Nano module like with the B01 Dev Kit.

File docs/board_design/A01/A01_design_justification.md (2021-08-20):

# A01 Design Justification

## A01 Schematic Design

I will step through the A01 schematic and highlight and explain the features and components that changed from A00. 

### Page 2 of A01 Schematic: Camera

<p align="left">
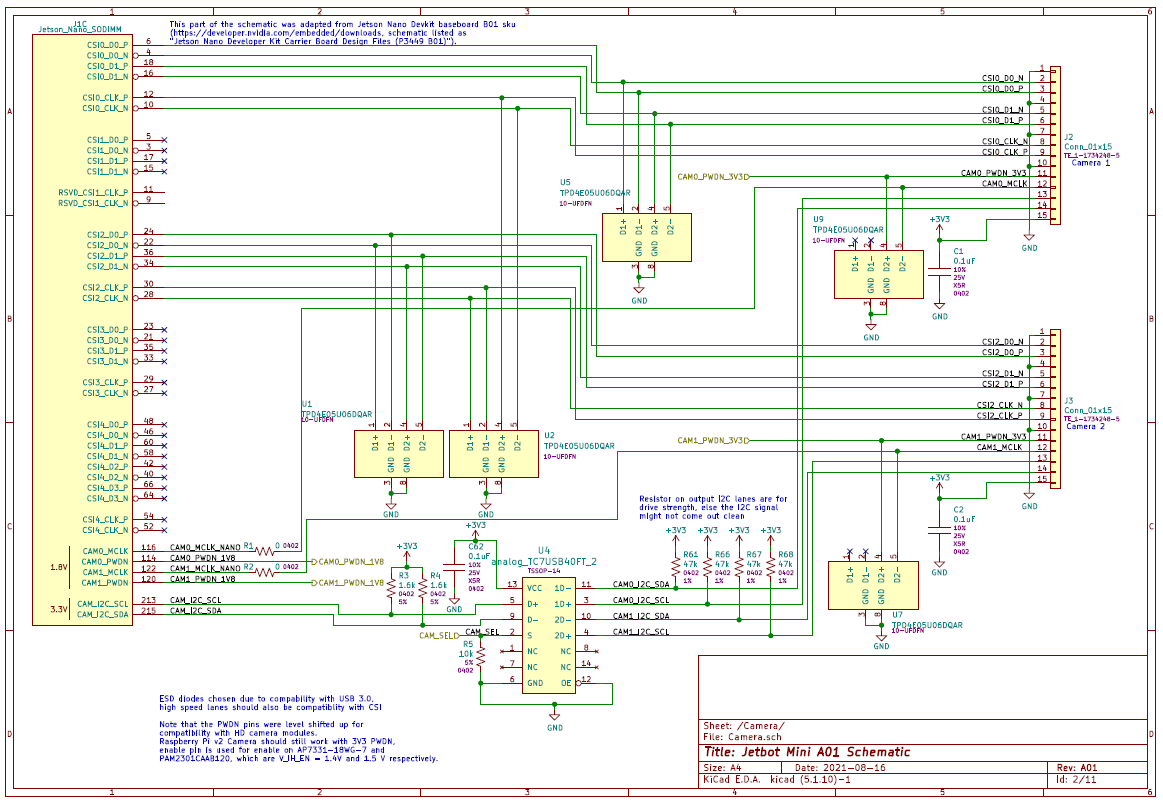
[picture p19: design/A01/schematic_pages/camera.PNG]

</p>

* The main change from A00 is the addition of R61, R66, R67, and R68 on the output of the camera mux U4. These extra pullups are to meet rise time requirements. The analog camera mux has finite series resistance that the I2C signals will encounter, and so the rising edges of the I2C signals after the mux are slower which can cause problems at higher I2C clock speeds. In addition, any I2C device connected will have parasitic capacitance, so the rising and falling edges of the I2C signals will not be sharp. The pullup resistors are there to provide extra drive strength to sharpen the edges. In the following image, the pullup resistors help the signal go from the first waveform, which is distorted, to a more sharp square wave. 

<p align="left">
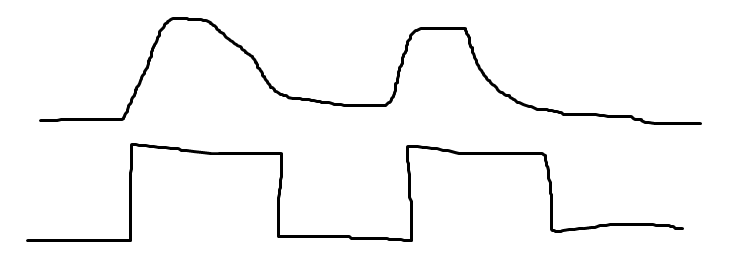
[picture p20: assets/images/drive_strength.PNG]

</p>

* The pullups are 47kohms as the drive strength should not be too high, as the Jetson Nano module has 2kohm pullups, so the weaker 47kohm resistors are to compliment the existing pullups. 

### Page 6 of A01 Schematic: Power_1

<p align="left">
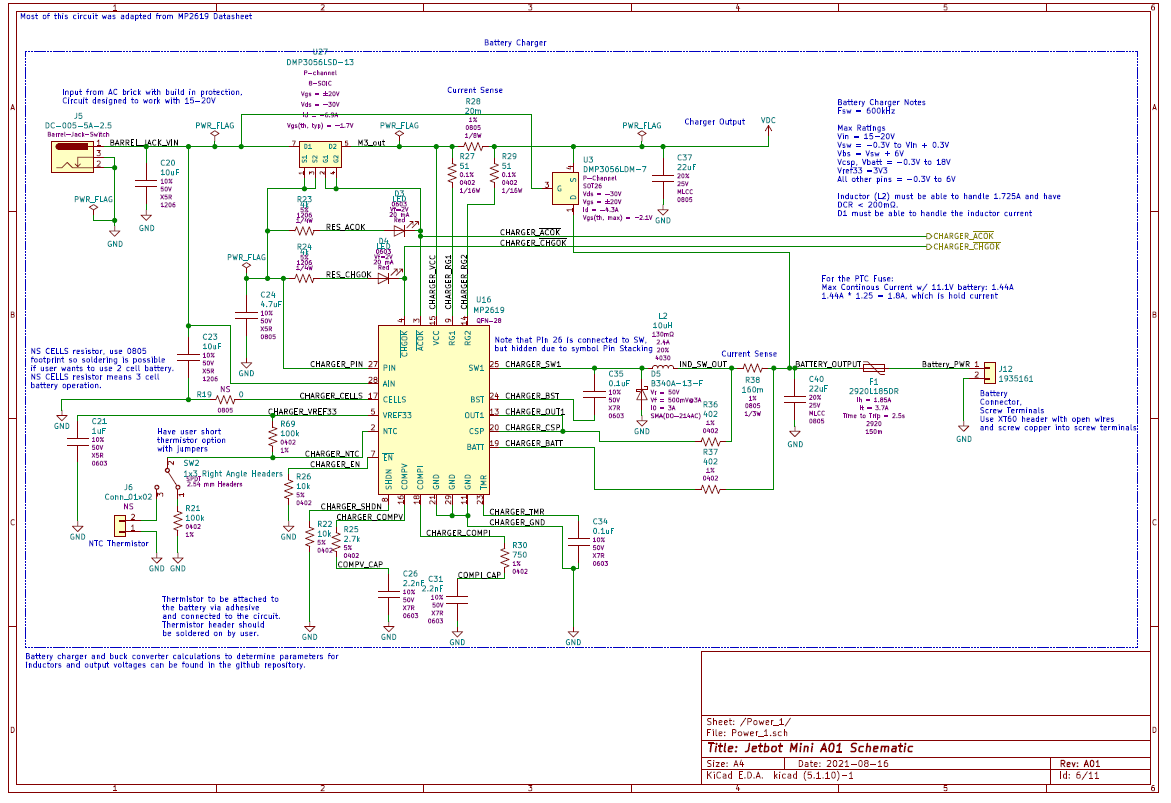
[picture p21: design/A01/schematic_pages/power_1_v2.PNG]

</p>

The main changes from A00 are as follows:
* R23 and R24 have been switched from 1kohm resistors to 4kohm resistors, as before at the max input voltage of 20V, the current through the LEDs would be 18 mA, which is cutting it close to the 20 mA max. Increasing the resistance adds more margin. 
* SW2 was added so that the user can charge the battery without needing an explicit separate NTC thermistor. 
* Note that this circuit is still WIP, as the chosen inductor and fuse need to be double checked and extensive validation has not been done on the boards yet. 

### Page 7 of A01 Schematic: Nano_IO

<p align="left">
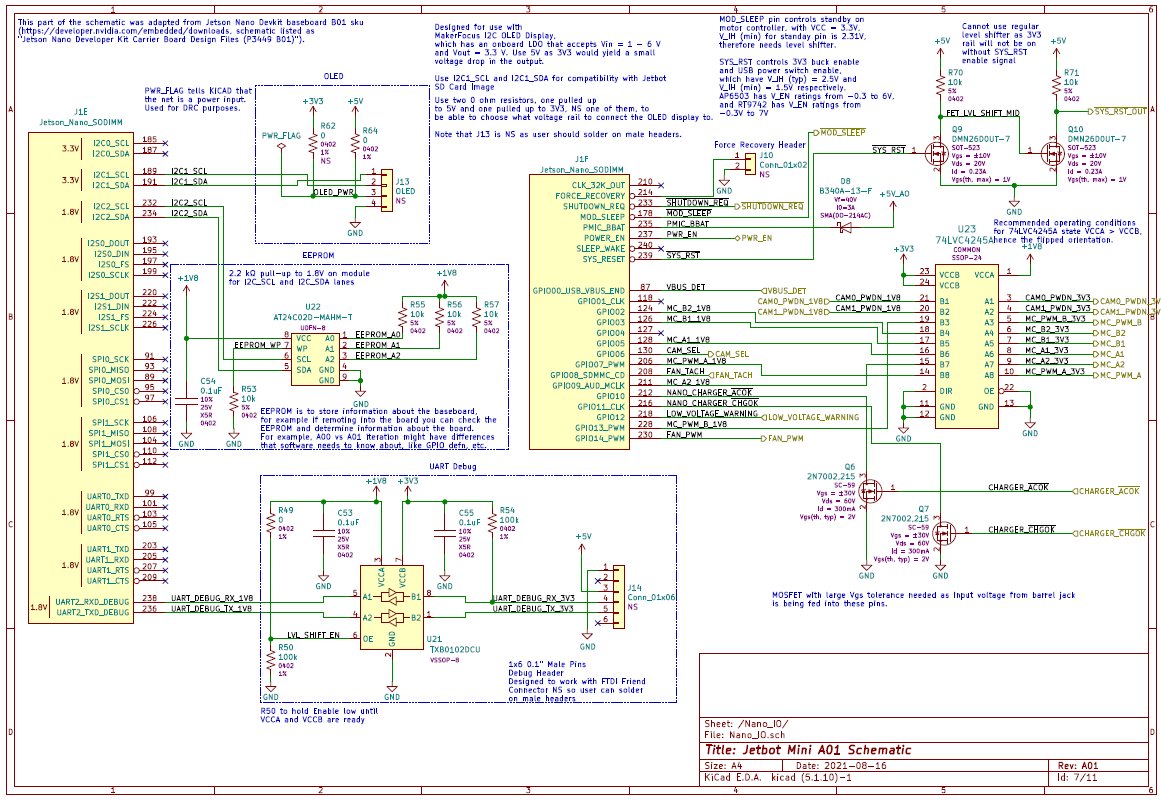
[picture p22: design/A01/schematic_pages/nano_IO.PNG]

</p>

The main changes from A00 are as follows:
* The OLED header now uses I2C1 lanes instead of I2C0 to comply with the Jetbot image without needing a software change to the stats.py file. In addition, a NS resistor is pulled up to 3V3 in case the user wished to uses a different OLED display with a different power requirement. 
* The RX and TX lanes of the UART debug header were switched to work with the FTDI friend; note that previously, RX on the baseboard would have been routed to RX on the FTDI friend, and TX to TX, which is incorrect. 
* A force recovery header option J10 was added for easier access to recovery mode; on A00, the only way to enter recovery mode was from stopping a boot using a serial connection over UART. 
* A transistor level shifter made from Q9, Q10, R70 and R71 was added to level shift SYS_RST from 1V8 to 5V so that it can properly turn on the 3V3 buck converter. 
  * The level shifter works as follows: SYS_RST will go high once module start-up sequence is completed. Initially when SYS_RST is low, Q9 is off, which means Q10 is ON, which pulls SYS_RST_OUT to ground. When SYS_RST goes high, Q9 is turned on, turning off Q10, which allows SYS_RST_OUT to be pulled high via R71 5V. Thus in the initially startup sequence, the 3V3 buck converter enable signal is pulled low, and once the startup sequence finishes and SYS_RST goes high, the enable signal will be pulled to 5V. 
  * 3V3 buck and USB power switch have V_IH = 2.5 V and V_IH = 1.5 V respectively, and AP6503 has V_EN ratings from -0.3 to 6V and RT9742 has V_EN ratings from -0.3 to 7V.
  * Cannot use one transistor, as when SYS_RST is pulled LOW, the transistor will be off meaning SYS_RST_OUT will be pulled high, which is the opposite of what we want.
* MC_A2 is now routed to GPIO09 instead of GPIO04, to bypass the software issue with GPIO04. Note that I need to consider rerouting all the motor control GPIO to GPIO on the 40 pin header for easier control. 

### Page 8 of A01 Schematic: Power_3

<p align="left">
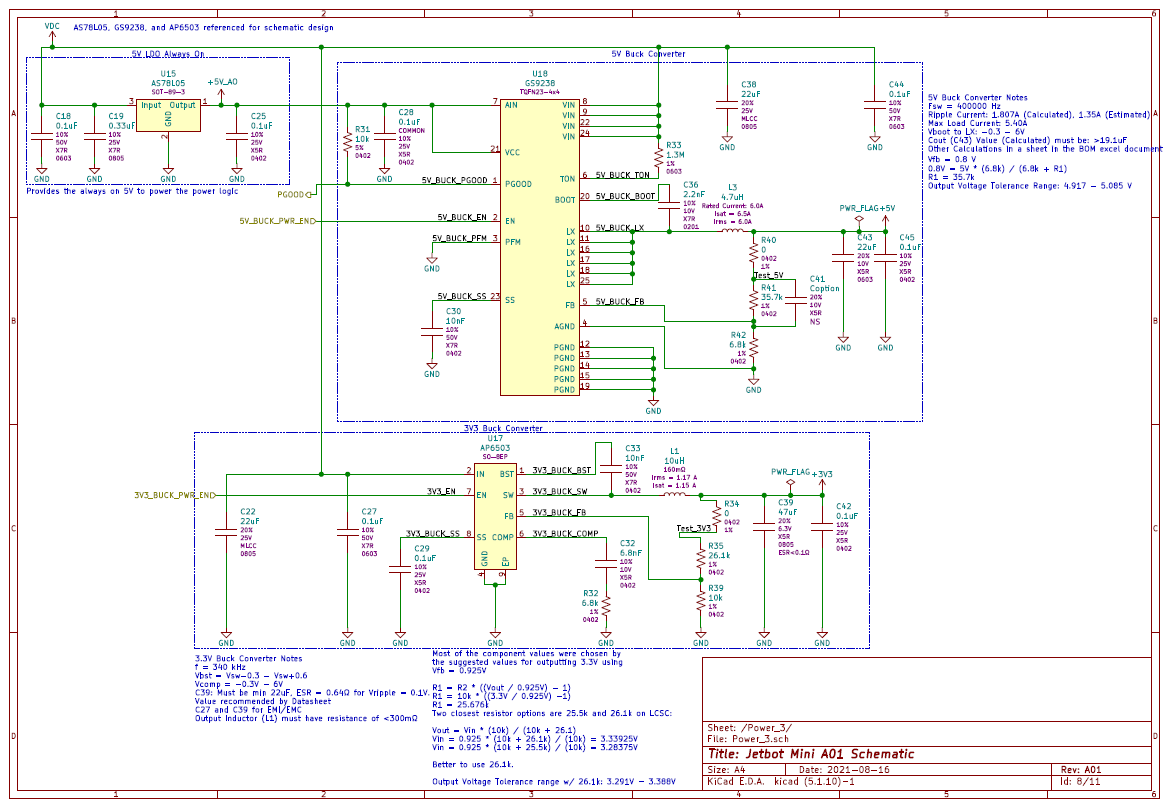
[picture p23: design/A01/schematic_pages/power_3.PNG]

</p>

The main changes from A00 are as follows:
* R39 has been changed from 5% tolerance to 1% tolerance to allow for more precise voltage output. Large tolerances can mean large errors in the feedback that result in wide output voltage ranges, which is not ideal. 
* R41 and R42 have been changed to resistor values that correctly output 5V based off of Vfb = 0.8 V. 
  * Typically to calculate the feedback network for a buck converter, the IC will have a fixed voltage Vfb, and so with a target output voltage, you can calculate resistor values using a simple resistor divider equation. I was not aware of this when designing A00. 
* Note that some of the capacitors need to be changed to higher voltage ratings, like C19, C38, and C36. 
* Note that the 5V regulator may be switched for the AP64501, as it is a more common package and the GS9238 is currently (As if August 2021) not widely available. That particular IC does not have a PGOOD signal, but the power sequencing can be satisfied with an RC circuit. Another option is to split the 5V rail amongst multiple buck converters to reduce the current load on any one buck converter.

### Page 9 of A01 Schematic Power_2

<p align="left">
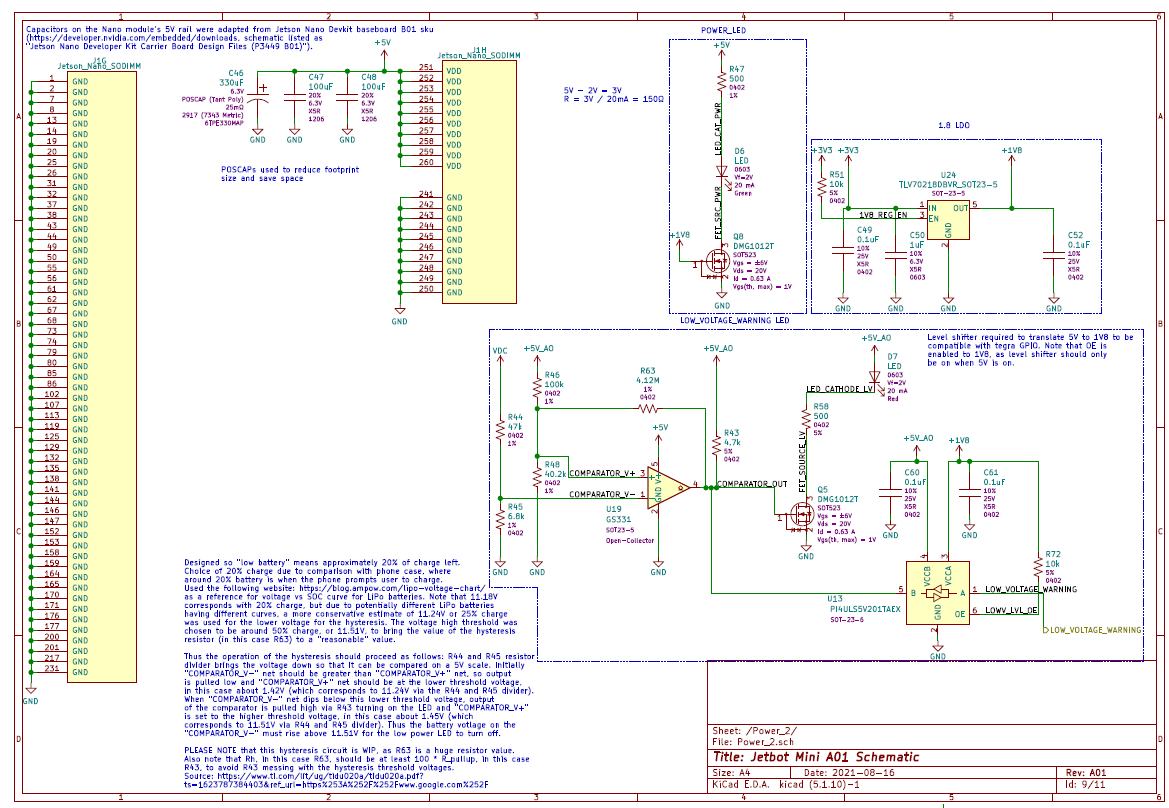
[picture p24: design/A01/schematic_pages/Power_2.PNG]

</p>

The main changes from A00 are as follows:
* Hysteresis was added to the comparator circuit that controls the low battery LED as we were seeing flickering on A00 baseboard. 
  * Hysteresis works as follows: a feedback resistor is connected from the output to the middle of the reference resistor divider. This additional resistor, in this case R63, will be added in parallel to R46 when the output is pulled high, and added in parallel to R48 when the output is pulled low. This sets two voltage thresholds; once the voltage dips below the first threshold and turns the LED on, the voltage threshold that the input voltage needs to cross to turn the LED off is HIGHER than the first voltage threshold. This prevents multiple transitions and should stop the LED from flickering. The following video shows the flickering LED:

https://user-images.githubusercontent.com/46247601/129977092-1d205fae-2e41-4213-b8e5-6699081f7fba.mp4

* In addition, the A00 baseboard voltage threshold for low voltage is 7.5 V, which is WAAAAY too low for the chosen batteries. I did not quite understand [state of charge vs voltage curves](https://blog.ampow.com/lipo-voltage-chart/); the batteries that I have should never be discharged below 9.6 V and should not be charged above 12.6 V, and so the fact that the LED indicates that you should charge the battery once it reaches 7.5 V means that you are damaging the battery. I have fixed the thresholds for A01 to be so that if the battery voltage dips below 11.18 V, or around 25% charge, the LED will turn on, and will turn off when the battery voltage rises above 11.51 V, or 50% charge. 

> Note that the current hysteresis circuit has a feedback resistor of 4.12Mohms, which is huge and thus any difference in resistance due to tolerances might greatly affect the voltage thresholds. This circuit needs to be looked into further. 

* The resistors R47 and R58 that limit current from the LEDs were increased from 150 ohms to 500 ohms to be safer. 

### Page 10 of A01 Schematic Power Logic

<p align="left">
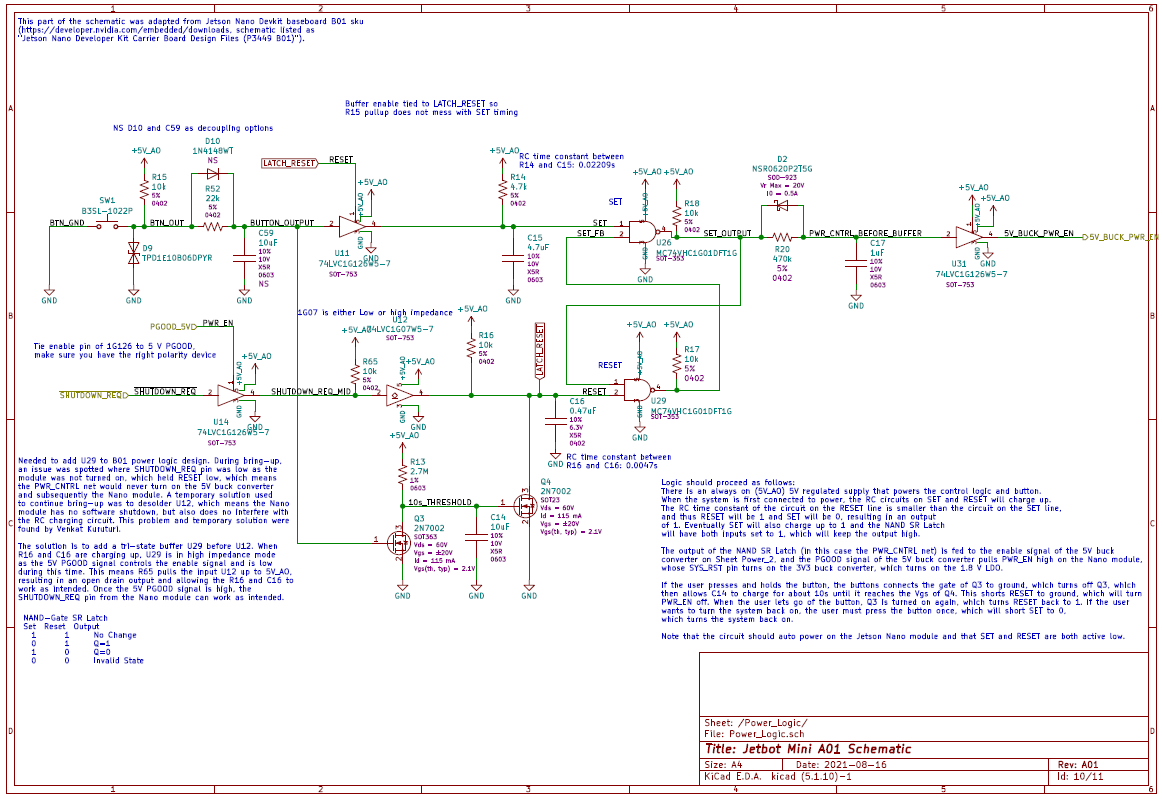
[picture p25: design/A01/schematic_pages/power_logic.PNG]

</p>

The main changes from A00 are as follows:
* How the power Power Logic should proceed is explained on the A01 schematic. 
* An additional tri-state buffer, U14, was added in between the SHUTDOWN_REQ signal and the U12 buffer so that SHUTDOWN_REQ does not affect the RESET signal during the startup sequence. 
* Note that R13 and C14 should be optimized further, as R13 is a huge resistor and any change due to tolerance might result in a large range of shutdown times. Smaller resistor values with a different RC ratio should be explored.

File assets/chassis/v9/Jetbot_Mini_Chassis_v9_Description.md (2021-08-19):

# Jetbot Mini Chassis v9

<p align="left">

</p>

This was the chassis used to test the A00 Baseboard on the LEGO roads, as it was overall the smallest and most balanced chassis design.  

## Specifications

| Field | Value | Unit |
| :--- | :--- | :--- |
| Weight | 397 | g | 
| Height | 108 | mm |
| Width | 53 | mm |
| Length | 95 | mm |
| Max Length | 127 | mm |
| Center of Mass Height | 48 | mm | 
| Max Speed Around Turn | ~0.46 | m/s |

Calculations are explained in [Chassis Documentation](https://github.com/NVIDIA-AI-IOT/jetbot_mini/tree/main/docs/chassis). 

## Pololu Parts

If you would like to use the same Pololu CAD files that I did to assemble the chassis, you can use the following links:
| Part | Link |
| :--- | :--- |
| Ball Caster | https://www.pololu.com/product/950 |
| Wheels | https://www.pololu.com/product/1088 |

To download the CAD files, scroll down to the ribbon headers, click "Resources", and step files should be listed under "File Downloads".

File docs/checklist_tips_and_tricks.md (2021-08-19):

# General Checklist and Tips and Tricks

These are some tips and tricks, as well as things to check when designing schematics, layout, and general design. 

## General Tips

* Be satisfied in a day's work! Pushing yourself to work harder and longer is not sustainable. 
* Always reach out for help if you need; even if the question is simple, it might save lots of time if you tried to search for answers yourself. 
* Be specific with you plan out your daily schedule.
* Make sure you fully understand feedback and suggestions!
* Always be humble and suspicious of your work!
* Always be wary of copied or referenced designs, whether it be previous work or documentation like datasheets; there might be problems or optimizations of that design that you might not know about. 
  * Always make sure you fully understand any design that you are copying or referencing, so you can properly test and debug the result and integrate it properly with the rest of your design. 
* Be careful of licenses when using open source designs and projects. 

## Schematic Tips

* **Every single component and every single specification of that component needs to have a reason and purpose!**
* LABEL ALL NETS, ALWAYS!!! It helps with readability and also when you layout your board, you will know what each signal and trace is supposed to be. 
* Always check the voltage levels that pins can accept. 
  * For the A00 baseboard, the signal controlling the buck converter enable pin was too low voltage.
* Print out or go through your schematic once you finish the design, and double check all calculations, label voltages at all nodes, and check current through each point wherever possible. This will help you with understanding the circuit, checking voltage acceptance levels, and make sure the design is tight. 
* 0.1 uF capacitors are often used at the input of power rails to help deal with sudden current requirements. 
* Check resistor and capacitor tolerances for things like RC time constants and circuits that require exact outputs or thresholds, like feedback networks and comparator circuits. 
* Avoid QFN packages for transistors; they are tiny and difficult to solder!
* Add test points wherever possible to the schematic to test signals during bring-up and validation. 
* Diodes, Holtek, Richteck, Silergy, and UPI are good companies to use when looking for buck converters. 
* Check manufacturer websites for MLCC specs like ripple current, ESR, and ESL if they are not on the datasheets (which they often explicitly stated for your exact part).
* Check discharge paths for all capacitors, make sure you understand their behavior!
* Make sure to check tolerances on important specs like Vgsth for transistors, as they may vary from part to part and lead to errors. 
* Double check capacitor voltage ratings! A good rule of thumb is to have a voltage rating double of what you expect the voltage at the cap to be, as factors like voltage ripple and noise can destroy an improperly designed capacitor. 

## Layout Tips

* **Every single component placement, silkscreen identifier, and via needs to have a purpose. Routing should be clean and look organized!**
* Make sure to maintain neat trace paths, adopt a “highway” plan where traces run vertically and horizontally and neatly across the board, and take traces from those highways. 
* Avoid sharp corners on traces and power places (fillet the edges), as they can cause acid traps and impedance issues.
* When a trace enters a via, make sure it enters at a clean 90 degree angle. 
* **Make sure everything hits the manufacturing house specs!! Things like via size, trace distance from edge of the board, minimum trace width, etc. Refer to stackup for calculating diff pair impedances.**
* Place IO connectors first and make sure to check spacing from other connectors. 
* You can place footprints ontop of other footprints to stuff different components. 
* Capacitors used to filter out noise and used for decoupling should be placed as close as possible to the relevant power rails / components. 
* Avoid thin power planes, as this increases resistance for your current path. 
* Things like buttons and headers should be spaced equally from each other, with neat silkscreen labels. Make sure headers line up with standard sets of headers so you can cut and place headers easily. 
* Void planes underneath ESD diodes and pads for high speed signals, as the planes can add additional parasitic capacitance. Be careful though, as voiding can also mean not having a reference plane for your high speed signals. 
* For high speed signals, you start to get transmission line effects like reflections, so be careful!
* Avoid stubs in your design!

## Bring-up Tips

* When probing or soldering probe wires to the board, make sure exposed wires are taped and insulated. 
* Wires that are connected to the board for probing purposes should be less than 1 cm. 
  * The shorter the wire, the cleaner you will be able to observe the signal, as there will be less resistance, reflection and coupled noise. 
* Oscilloscope probes are internally grounded, so often you only need to connect the ground for one probe if you are using multiple. 
  * Use MATH functions to get voltages across components if necessary, although often a multimeter is best for this job.
  * Be careful if you expect a lot of current in the signal, connect more ground paths if this is the case. 
* Make sure that the ground loop for the probe is small, otherwise the probe will pick up more noise. 

## Manufacturing and Gerber Out Checklist

* **Always check your GERBER files before getting your design manufacturing; see if you spot any issues and do a final check!**
* Select impedance control option for PCBs with high speed signals!!

## Debugging Tips

* **NEED TO UNDERSTAND THE CIRCUIT BEFORE YOU START PROBING STUFF AND THE RESISTORS, INTUITIVELY UNDERSTAND THE SYSTEM, AND IF YOU DON’T UNDERSTAND, THEN MODEL IT OR ASK FOR HELP!**
* Debugging also comes down to strong fundamentals and simply being exposed to lots of different circuit topologies. You will get better with experience. 
* Root cause isolation: when faced with a serious bug, write down all the possible causes for the problem. Then step through that list. You will be more organized and also feel a sense of progression, which is invaluable as during debugging, it is easy to get frustrated because you might be spending long periods of time not making much progress. 
* Save error files in text files rather than taking screenshots. 

## Presentation Tips

* Don't use words like "cheap", use words like "inexpensive" instead. 
* Know your audience, have empathy, don't try to blast jargon at them. 
* Don't read off slides!!!

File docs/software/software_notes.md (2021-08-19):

# Software Notes

## Arduino MotorHAT Library

This [library](https://github.com/adafruit/Adafruit-Motor-HAT-Python-Library) is used to control the motors in the original Jetbot code, and is normally controlled with I2C. I cut all dependence on the Adafruit_PWM_Servo_Driver.py file, deleted the module from the __init__.py file, and replaced the I2C commands in Adafruit_MotorHAT_motors.py with GPIO ones from the Jetson-GPIO library. 

## Jetson-GPIO Library

This [library](https://github.com/NVIDIA/jetson-gpio) uses terminal commands similar to the GPIO commands outlined in [this file](https://github.com/NVIDIA-AI-IOT/jetbot_mini/blob/main/docs/board_design/A00/bringup_rework/A00_bringup_rework.md), but packages everything nicely into a set of commands. The only file I changed here was the gpio_pin_data.py file, where I added the motor GPIO to the Jetson Nano pin descriptions, as they were not there before. 

## Jetbot Library

This [library](https://github.com/NVIDIA-AI-IOT/jetbot) houses commands that the Jupyter Notebook examples reference. I cut out I2C dependence in the motor.py and robot.py files, and made sure to keep most of the classes and commands intact. 

## General Notes

* I believe the trailets class defines types for variables and allows for the cool interactive elements like buttons and sliders that Jupyter Notebook creates. 
* Commands with underscores are not meant to be called by the user, only by the code and other libraries. This is a python convention.

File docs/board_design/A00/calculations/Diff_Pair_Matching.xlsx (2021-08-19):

Stackup Properties
Dielectric Thickness / Distance between signals and reference ground plane (mm) | 0.11
Dielectric Constant | 4.29
 |  | Diff Pair Target Impedance (ohms) | Tolerance | Max length (mm) | Min Distance from other diff pairs, high speed, planes, capacitors (mm) | Calculated Width | Calculated intra-spacing | Calculated Diff pair Impedance (Saturn PCB) | Calculated SE Impedance (Saturn PCB) | Lengths
USB 3.0 | RX | 85-90 | 10% | 152.3 | 0.44 | 0.2 | 0.25 | 83.816 | 44.308 | 51.354
 | USB1 | 85-90 | 10% | 152.3 | 0.44 | 0.2 | 0.25 | 83.816 | 44.308 | 58.646
 | TX | 85-90 | 10% | 152.3 | 0.44 | 0.2 | 0.25 | 83.816 | 44.308 | 36.19
USB 2.0 | USB0 | 90 | 15% |  |  | 0.2 | 0.25 | 83.816 | 44.308 | 58.45
CSI | CSI0_D0 | 90-100 | 10% |  | 0.44 | 0.2 | 0.25 | 83.816 | 44.308 | 21.676
 | CSI0_D1 | 90-100 | 10% |  | 0.44 | 0.2 | 0.25 | 83.816 | 44.308 | 21.723
 | CSI0_CLK | 90-100 | 10% |  | 0.44 | 0.2 | 0.25 | 83.816 | 44.308 | 21.66
 | CSI2_D0 | 90-100 | 10% |  | 0.44 | 0.2 | 0.25 | 83.816 | 44.308 | 25.721
 | CSI2_D1 | 90-100 | 10% |  | 0.44 | 0.2 | 0.25 | 83.816 | 44.308 | 25.721
 | CSI2_CLK | 90-100 | 10% |  | 0.44 | 0.2 | 0.25 | 83.816 | 44.308 | 25.689

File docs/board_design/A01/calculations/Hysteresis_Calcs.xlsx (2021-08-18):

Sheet: MOSFET Hysteresis Method
Vin | R1 | R2 | Vout | Vcc
11.24 | 47000 | 10000 | 1.971929825 | 5
11.51 | 47000 | 10000 | 2.019298246
Rx | Ry_target | Ry2
47000 | 30607.18424 | 31840.49441
 | Ry
 | 790188.7979

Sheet: Pure Resistor Hysteresis Method
Vin | R1 | R2 | Vout | Vcc
11.24 | 47000 | 6800 | 1.420669145 | 5
11.51 | 47000 | 6800 | 1.454795539
Rx | Ry | Rh
100000 | 40072.98199 | 4162962.963
R1 | R2 | Ry | Rh | Ry_eq | Rx_eq | V_L | V_H | Vbat_L | Vbat_H
47000 | 10000 | 66500 | 4120000 | 65443.68804 | 97630.33175 | 1.977823658 | 2.025829086 | 11.27359485 | 11.54722579
47000 | 6800 | 40200 | 4120000 | 39811.54752 | 97630.33175 | 1.423757487 | 1.458314708 | 11.26443424 | 11.53784284
47000 | 4700 | 25500 | 4120000 | 25343.14317 | 97630.33175 | 1.010950521 | 1.035488155 | 11.12045573 | 11.3903697

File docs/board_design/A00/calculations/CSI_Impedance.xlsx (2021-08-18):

Name | Length N (mm) | Length P (mm) | Difference (mm) | Intra-Pair Skew (ps) | Average Length | Inter-Pair Skew 1 (ps) | Inter-Pair Skew 2 (ps) | Comments
CSI0_D0 | 20.931 | 21.667 | 0.736 | 4.052913228 | 21.299 | 0.2808404547 | 0.7516612169
CSI0_D1 | 20.977 | 21.723 | 0.746 | 4.107979984 | 21.35 | 0.2808404547 | 1.032501672
CSI0_CLK | 20.914 | 21.411 | 0.497 | 2.736817764 | 21.1625 | 0.7516612169 | 1.032501672 | Need to add 1.6 * 2 for the vias?
CSI2_D0 | 25.473 | 25.722 | 0.249 | 1.37116222 | 25.5975 | 0 | 1.550129176
CSI2_D1 | 25.473 | 25.722 | 0.249 | 1.37116222 | 25.5975 | 0 | 1.550129176
CSI2_CLK | 24.943 | 25.689 | 0.746 | 4.107979984 | 25.316 | 1.550129176 | 1.550129176
Conversion Factor (ps / mm) | er
5.506675581 | 4.29
Reference for t_pd: | https://www.analog.com/media/en/training-seminars/tutorials/MT-094.pdf

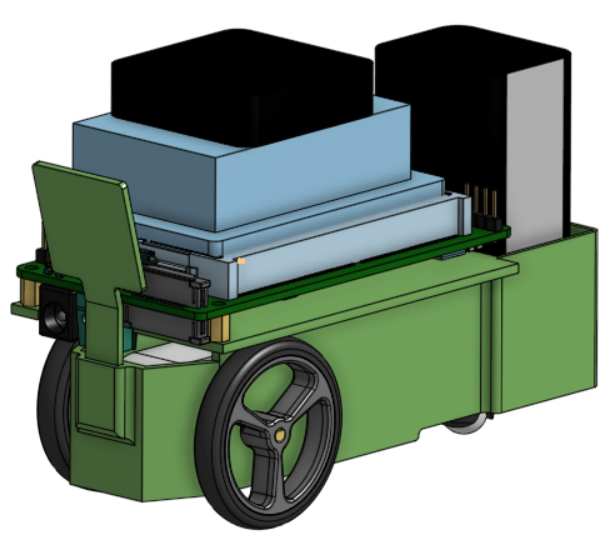
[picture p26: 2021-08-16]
assets/images/chassis/Jetbot_Mini_v6_Horizontal_Chassis.PNG

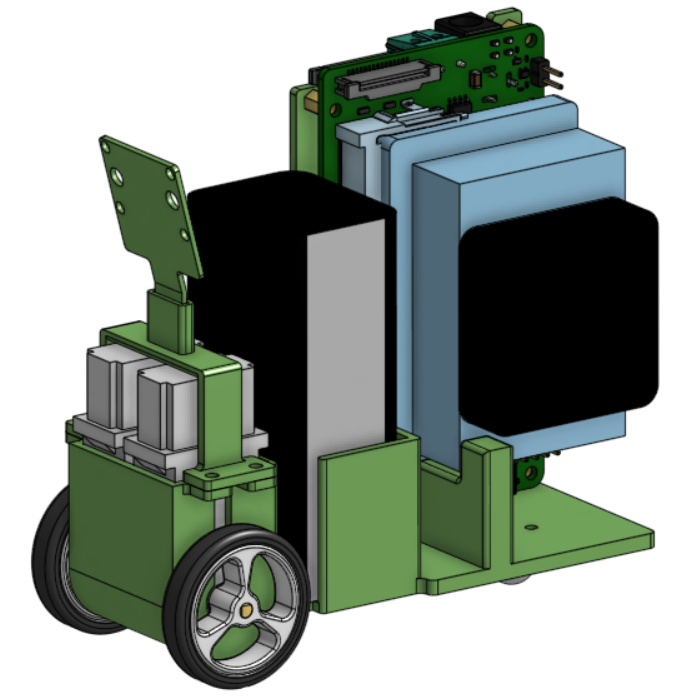
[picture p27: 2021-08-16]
assets/images/chassis/Jetbot_Mini_v8_Vertical_Chassis.PNG

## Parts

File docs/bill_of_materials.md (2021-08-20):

# Bill of Materials

This page lists everything a user would need to build the A00 Jetbot Mini. 

> As mentioned in the overall README, the A00 baseboard is not recommended for manufacture as the boards have not been fully validated and require an extensive rework to work properly. A01, the next iteration of the schematic, is currently being worked on.

Some of the parts are 3D printed, so please refer to the [3D printing documentation](3d_printing_guide.md) for tips on printing, and [here](https://github.com/NVIDIA-AI-IOT/jetbot_mini/tree/main/assets/chassis) for the chassis CAD files. 

## Common Parts

Please note that these are the parts that I build A00 Jetbot Mini with, and the parts are subject to change and price optimizations.  
Also note that these are the prices as of August 17th, 2021, and are subject to change due to availability. 

| Part | Quantity | Cost Per Unit | Total Cost | URL | Notes |
| :--- | :--- | :--- | :--- | :--- | :--- |
| A00 Baseboard | 1 | $72 | $72 | -- | Note that this is with 10 boards ordered; $72 was the cost per fully assembled board. |
| Jetson Nano | 1 | $99 | $99 | [NVIDIA](https://developer.nvidia.com/embedded/jetson-nano-developer-kit) | -- | 
| Micro SD Card | 1 | $10.99 | $10.99 | [Amazon](https://www.amazon.com/SAMSUNG-Select-microSDXC-Adapter-MB-ME64HA/dp/B08879MG33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) | Sizes over 64 GB should work. |
| Power Supply | 1 | $18.99 | $18.99 | [Amazon](https://www.amazon.com/SoulBay-Universal-100-240VAC-Transformer-Electronics/dp/B086JLYBQ7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) | This is a nice adjustable power supply that I used to run the Jetson Nano module and charge the battery. Note that there are cheaper options out there, and any supply from 15-20V should be sufficient to charge the battery. Just make sure the inner hole is 2.5mm! |
| Motors | 2 | $5.49 | $10.98 | [Pololu](https://www.pololu.com/product/1124) | I chose to use Pololu motors as they are a reputable robotics brand and popular amongst makers. |
| Wheels | 1 | $2.95 | $2.95 | [Pololu](https://www.pololu.com/product/1088) | Get creative with different colored wheels! Note that when you buy wheels, they come in packs of 2. |
| Ball Caster | 2 | $1.99 | $3.98 | [Pololu](https://www.pololu.com/product/950) | -- |
| Battery | 1 | $27.99 | $27.99 | [Amazon](https://www.amazon.com/GOLDBAT-Softcase-m4-fpv250-Shredder-Helicopter/dp/B07ZFDJWR1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) | Note that each order comes with two batteries. |
| Battery XT60 Connectors | 1 | $6.90 | $6.90 | [Amazon](https://www.amazon.com/HOBBYMATE-XT60H-Sheath-Female-Connectors/dp/B07KTM1T7G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) | Note that each order comes with two of the female connectors needed to connect to the chosen battery. |  
| OLED Display | 1 | $9.59 | $9.59 | [Amazon](https://www.amazon.com/MakerFocus-Display-SSD1306-3-3V-5V-Arduino/dp/B0761LV1SD) | Note that each order comes with two OLED displays. 
| Wifi | 1 | $12.99 | $12.99 | [Amazon](https://www.amazon.com/dp/B07PB1X4CN//ref=cm_sw_su_dp) | These are the Wifi dongles that I used, but there are cheaper options out there. |
| Camera | 1 | $29.15 | $29.15 | [Amazon](https://www.amazon.com/dp/B07T43K7LC//ref=cm_sw_su_dp) | I've only tested with the IMX219-160 camera for Jetbot Mini, but the other options from the [Jetbot BOM](https://github.com/NVIDIA-AI-IOT/jetbot/blob/master/docs/bill_of_materials.md) should work as well. |
| Chassis Body | 1 | -- | -- | [STL File](https://github.com/NVIDIA-AI-IOT/jetbot_mini/blob/main/assets/chassis/v9/v9_stl/Chassis_Body_v9_Vertical.stl) | Chassis v9 files linked. |
| Camera Mount | 1 | -- | -- | [STL File](https://github.com/NVIDIA-AI-IOT/jetbot_mini/blob/main/assets/chassis/v9/v9_stl/Camera_Mount_v1.stl) | Chassis v9 files linked. |
| Motor Latch | 1 | -- | -- | [STL File](https://github.com/NVIDIA-AI-IOT/jetbot_mini/blob/main/assets/chassis/v9/v9_stl/Motor_Latch_v2.stl) | Chassis v9 files linked. | 

## Assembly Hardware

| Part | Quantity per Jetbot Mini | Cost Per Jetbot Mini | Total Cost | URL | Notes |
| :--- | :--- | :--- | :--- | :--- | :--- |
| M2.5 Standoffs, Bolts and Screws | 12 | $0.56 | $7.99 | [Micro Center](https://www.microcenter.com/product/622303/micro-connectors-assorted-m25-standoff-kit-114-pieces) | I picked up this kit from Micro Center, there might be cheaper options on Amazon and other retailers. Used to secure baseboard to chassis body. |
| Headers for OLED and IO | 16 | $0.08 | $5.99 | [Amazon](https://www.amazon.com/DEPEPE-2-54mm-Headers-Arduino-Prototype/dp/B074HVBTZ4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) | Requires soldering to connect to baseboard. |
| Bolts and Nuts | 16 | $0.19 | $3.99 | [Micro Center](https://www.microcenter.com/product/623879/inland-bolt-set-330-pieces) | I picked up this kit from Micro Center, there might be cheaper options on Amazon and other retailers. Used for camera mount and securing motor latch. |
| Wires | -- | -- | $14.99 | [Amazon](https://www.amazon.com/TUOFENG-Wire-Solid-different-colored-spools/dp/B07TX6BX47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) | Used for rework, debugging and connecting to motors to baseboard. I used 22 awg for connecting the motors, and 28 awg for rework and debugging. |

## Useful Tools
These are the tools I used to build the Jetbot Mini. 

| Tool | Price | URL | Notes |
| :--- | :--- | :--- | :--- |
| Soldering Iron | $104.95 | [Amazon](https://www.amazon.com/Hakko-FX888D-23BY-Digital-Soldering-Station/dp/B00ANZRT4M) | I love this soldering iron, but it its too pricey I can also recommend the X-Tronic 3020-XTS or Weller WLC100 |
| Solder | $8.99 | [Amazon](https://www.amazon.com/YI-LIN-Electrical-Soldering-0-22lbs/dp/B08RHMPJW3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) | This is the solder I used, but it is leaded solder so use it at your own risk. Always have a fume extractor and be in a well-ventilated area. You can also use unleaded solder. |
| Fume Extractor | $59.99 | [Amazon](https://www.amazon.com/Xytronic-0608426DLX-426DLX-Fume-Extractor/dp/B0007ZLH4Q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) | This is the fume extractor I used, but there are cheaper options on Amazon. |
| Third Hand | $19.99 | [Amazon](https://www.amazon.com/KOTTO-Soldering-Magnetic-Flexible-Workshop/dp/B083SFWLW7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) | This is not a necessity but extremely useful if you can afford it. It helps a lot with holding what you are soldering, like wires, resistors, and capacitors in place. If you cannot afford one, I often use books, boxes or rubber bands to hold things steady while I solder. |
| Multimeter | $76.95 | [Amazon](https://www.amazon.com/Amprobe-AM-530-Electrical-Non-Contact-Temperature/dp/B007FZFE9K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) | I used this multimeter, but there are plenty of good quality budget options out there. |
| Charging Bag | $10.99 | [Amazon](https://www.amazon.com/DerBlue-Fireproof-Explosionproof-Battery-Bag%EF%BC%88185x75x60mm%EF%BC%89/dp/B01GCHBQJS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) | In case something goes wrong during charging, keeping your battery in a bag like this while charging is a good safety measure. |
| Wires cutters | $13.75 | [Amazon](https://www.amazon.com/Hakko-CSP-30-1-Stripper-Maximum-Capacity/dp/B00FZPHMUG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) | These are the pair that I used, but there are many good options out there. A good quality set of wire cutters can last you years, so don't be afraid to invest a little. I've had my pair for 3 years and its served me well. |
| Diagonal Cutters | $7.47 | [Amazon](https://www.amazon.com/Hakko-CHP-170-Micro-Cutter/dp/B00FZPDG1K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) | These are the pair that I use to cut the male and female headers. There are plenty of other good options out there. |

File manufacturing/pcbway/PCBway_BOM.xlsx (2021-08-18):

Item # | *Designator | *Qty | Manufacturer | *Mfg Part # | Description / Value | *Package/Footprint | Type | Your Instructions / Notes
1 | C1, C2, C3, C5, C7, C8, C10, C12, C13, C25, C28, C29, C42, C45, C49, C51, C52, C53, C54, C55, C56, C57, C58, | 23 | Samsung Electro-Mechanics | CL05A104KA5NNNC | CAP CER 0.1uF 25V 10% X5R | 0402 | SMD | Datasheets: https://media.digikey.com/pdf/Data%20Sheets/Samsung%20PDFs/CL05A104KA5NNNC.pdf
2 | C4, C6, C9, C14, | 4 | Samsung Electro-Mechanics | CL10A106KP8NNNC | CAP CER 10uF 10V 10% X5R | 0603 | SMD
3 | C11, | 1 | Panasonic Electronic Components | 6TPG150MZG | CAP TANT POLY 150uF 6.3V 20% | 1411 | SMD
4 | C15, | 1 | Samsung Electro-Mechanics | CL10A475KP8NNNC | CAP CER 4.7uF 10V 10% X5R | 0603 | SMD
5 | C16, | 1 | Taiyo Yuden | JMK105BJ474KV-F | CAP CER 0.47UF 6.3V 10% X5R | 0402 | SMD
6 | C17, C21, C50 | 1 | Samsung Electro-Mechanics | CL10A105KB8NNNC | CAP CER 1UF 50V 10% X5R | 0603 | SMD
7 | C18, C27, C34, C35, C44, | 5 | AVX Corporation | 06035C104JAT2A | CAP CER 0.1UF 50V 5% X7R | 0603 | SMD
8 | C19, | 1 | Murata Electronics | GRM21BR71E334KA01L | CAP CER 0.33UF 10% 25V X7R | 0805 | SMD
9 | C20, C23, | 2 | Samsung Electro-Mechanics | CL31A106KBHNNNE | CAP CER 10UF 50V 10% X5R | 1206 | SMD
10 | C22, C37, C38, C40, | 4 | Samsung Electro-Mechanics | CL21A226MAYNNNE | MLCC 22UF 25V 20% X5R | 0805 | SMD
11 | C24, | 1 | Samsung Electro-Mechanics | CL21A475KBQNNNE | CAP CER 4.7UF 50V 10% X5R | 0805 | SMD
12 | C26, C31, | 2 | Samsung Electro-Mechanics | CL10B222KB8NNNC | CAP CER 2200PF 50V 10% X7R | 0603 | SMD
13 | C30, C33, | 2 | Samsung Electro-Mechanics | CL05B103KB5NNNC | CAP CER 10000PF 50V 10% X7R | 0402 | SMD
14 | C32, | 1 | Würth Elektronik | 885012205011 | CAP CER 6800PF 10V 10% X7R | 0402 | SMD | datasheet: https://katalog.we-online.de/pbs/datasheet/885012205011.pdf
15 | C36, | 1 | Murata Electronics | GRM033R71A222KA01D | CAP CER 2200PF 10V 10% X7R | 0201 | SMD
16 | C39, | 1 | Yageo | CC0805MKX5R5BB476 | CAP CER 47UF 6.3V 20% X5R | 0805 | SMD
17 | C43, | 1 | Samsung Electro-Mechanics | CL10A226MP8NUNE | CAP CER 22UF 10V 20% X5R | 0603 | SMD
18 | C46, | 1 | Panasonic Electronic Components | 6TPE330MAP | CAP TANT POLY 330UF 6.3V | 2917 | SMD
19 | C47, C48, | 2 | Samsung Electro-Mechanics | CL31A107MQHNNNE | CAP CER 100UF 6.3V 20% X5R | 1206 | SMD
20 | D1, D9, | 2 | Texas Instruments | TPD1E10B06DPYR | TVS DIODE 5.5V 14V | 0402 | SMD
21 | D2, | 1 | ON Semiconductor | NSR0620P2T5G | DIODE SCHOTTKY 20V 500MA | SOD-923 | SMD
22 | D3, D4, D7, | 3 | Lite-On Inc. | LTST-C191KRKT | LED RED CLEAR | 0603 (1608 Metric) | SMD
23 | D6, | 1 | Lite-On Inc. | LTST-C191KGKT | LED GREEN CLEAR | 0603 (1608 Metric) | SMD
24 | D5, D8, | 2 | Diodes Incorporated | B340A-13-F | DIODE SCHOTTKY 40V 3A SMA | DO-214AC, SMA | SMD
25 | F1, | 1 | Littelfuse Inc. | 2920L185DR | PTC RESET FUSE 33V 1.85A | 2920 (7351 Metric), Concave | SMD
26 | J1, | 1 | TE CONNECTIVITY | 2309411-5 | DDR4 DIMM, SO DIMM Sockets, Small Outline (SO), Stack Height .315 in [8 mm], Right Angle Module Orientation, Surface Mount, Cable-to-Board |  | SMD | Not sure what to put for footprint, so just left blank, footprint can be found on this website: https://www.te.com/usa-en/product-2309411-5.html
27 | J2, J3, | 2 | TE Connectivity AMP Connectors | 1-1734248-5 | CONN FPC VERT 15POS 1.00MM SMD |  | SMD | Not sure what to put for footprint, so just left blank
28 | J4, | 1 | GCT | BG300-04-A-L-A | 4W, 2.54MM PTH SOCKET, SIL, SMT, |  | SMT | Not sure what to put for footprint, so just left blank
29 | J5, | 1 | XKB Connectivity | DC-005-5A-2.5 | DC Power Receptacle Jack 5A 2.5mm 6.5mm Through Hole AC/DC Power Plugs & Receptacles RoHS |  | Through Hole | Not sure what to put for footprint, so just left blank
30 | J7, | 1 | Amphenol ICC (FCI) | 10103594-0001LF | USB - micro B USB 2.0 Receptacle Connector 5 Position Surface Mount, Right Angle; Through Hole |  | Surface Mount, Right Angle; Through Hole | Not sure what to put for footprint, so just left blank
31 | J8, | 1 | Würth Elektronik | 692121130100 | USB-A (USB TYPE-A) USB 3.2 Gen 1 (USB 3.1 Gen 1, Superspeed (USB 3.0)) Receptacle Connector 9 Position Board Edge, Cutout |  | Through Hole, Right Angle | Not sure what to put for footprint, so just left blank
32 | J12, | 1 | Phoenix Contact | 1935161 | 2 Position Wire to Board Terminal Block Horizontal with Board 0.197" (5.00mm) |  | Through Hole | Not sure what to put for footprint, so just left blank
33 | L1, | 1 | Murata Electronics | LQH44PN100MP0L | FIXED IND 10UH 1.17A 160 MOHM | 1515 | SMD
34 | L2, | 1 | Sunlord | SWPA4030S100MT | 10uH ±20% 1.5A 130mΩ Power Inductors | 4030
35 | L3, | 1 | Sunlord | MWSA0603-4R7MT | 4.7uH ±20% 6A 33mΩ Power Inductors | SMD,6.6x7.1x3.0mm | SMD
36 | Q1, Q2, | 2 | Diodes Incorporated | DMN26D0UT-7 | MOSFET N-CH 20V 230MA | SOT523 | SMD
37 | Q3, Q4, | 2 | ON Semiconductor | 2N7002 | MOSFET N-CH 60V 115MA | SOT-23 | SMD | Datasheet: https://www.onsemi.com/pub/Collateral/NDS7002A-D.PDF
38 | Q5, Q8, | 2 | Diodes Incorporated | DMG1012T | MOSFET N-CH 20V 630MA | SOT-523 | SMD
39 | Q6, Q7, | 2 | Nexperia USA Inc. | 2N7002,215 | MOSFET N-CH 60V 300MA SOT-23 | SC-59 | SMD
40 | R1, R2, R34, R40, R49, R60, R61, | 7 | UNI-ROYAL(Uniroyal Elec) | 0402WGF0000TCE | 0Ω ±1% 1/16W 0402 Chip Resistor | 0402 | SMD
41 | R3, R4, | 2 | Yageo | RC0402JR-071K6L | RES SMD 1.6K OHM 5% 1/16W 0402 | 0402 | SMD
42 | R5, R6, R9, R10, R11, R12, R15, R16, R17, R18, R26, R31, R39, R42, R46, R48, R51, R53, R55, R56, R57, R59, | 22 | Stackpole Electronics Inc | RMCF0402JT10K0 | RES 10K OHM 5% 1/16W 0402 | 0402 | SMD
43 | R7, | 1 | Yageo | RC0402FR-071ML | RES SMD 1M OHM 1% 1/16W 0402 | 0402 | SMD
44 | R8, R21, R50, R54, | 4 | UNI-ROYAL(Uniroyal Elec) | 0402WGJ0104TCE | 100kΩ ±5% 1/16W Chip Resistor | 0402 | SMD
45 | R13, | 1 | KOA Speer Electronics, Inc. | RK73H1JTTD2704F | RES 2.7M OHM 1% 1/10W | 0603 | SMD
46 | R14, R43, | 2 | UNI-ROYAL(Uniroyal Elec) | 0402WGJ0472TCE | 4.7kΩ ±5% 1/16W Chip Resistor | 0402 | SMD
47 | R20, | 1 | UNI-ROYAL(Uniroyal Elec) | 0402WGJ0474TCE | 470kΩ ±5% 1/16W Chip Resistor | 0402 | SMD
48 | R23, R24, | 2 | LIZ Elec | CR1206J40102G | 1kΩ ±5% 0.25W Chip Resistor | 1206 | SMD
49 | R25, | 1 | UNI-ROYAL(Uniroyal Elec) | 0402WGJ0272TCE | 2.7kΩ ±5% 1/16W Chip Resistor | 0402 | SMD
50 | R27, R29, | 2 | Vishay Thin Film | FC0402E50R0BST1 | RES SMD 50 OHM 0.1% 1/20W 0402 | 0402 | SMD
51 | R28, | 1 | Yageo | RL0805FR-070R02L | RES 0.02 OHM 1% 1/8W 0805 | 0805 | SMD
52 | R30, | 1 | UNI-ROYAL(Uniroyal Elec) | 0402WGF7500TCE | 750Ω ±1% 1/16W Chip Resistor | 0402 | SMD
53 | R32, | 1 | Yageo | RC0402FR-076K8L | RES SMD 6.8K OHM 1% 1/16W | 0402 | SMD
54 | R33, | 1 | Yageo | RC0603FR-071M3L | RES SMD 1.3M OHM 1% 1/10W | 0603 | SMD
55 | R35, | 1 | Yageo | RC0402FR-0726K1L | RES SMD 26.1K OHM 1% 1/16W | 0402 | SMD
56 | R36, R37, | 2 | Yageo | RC0402FR-07402RL | RES SMD 402 OHM 1% 1/16W | 0402 | SMD
57 | R38, | 1 | Susumu | RL1220S-R16-F | RES 0.16 OHM 1% 1/3W | 0805 | SMD
58 | R41 | 1 | Yageo | RC0402FR-0756KL | RES SMD 56K OHM 1% 1/16W | 0402 | SMD
59 | R44, | 1 | Yageo | RC0402FR-075K1L | RES SMD 5.1K OHM 1% 1/16W | 0402 | SMD
60 | R45, | 1 | Yageo | RC0402FR-0718K7L | RES 18.7K OHM 1% 1/16W | 0402 | SMD
61 | R47, R58, | 1 | Yageo | RC0402JR-07150RL | RES SMD 150 OHM 5% 1/16W | 0402 | SMD
62 | SW1, | 1 | Omron Electronics Inc-EMC Div | B3SL-1022P | SWITCH TACTILE SPST-NO 0.05A 12V |  | SMD | Not sure what to put for footprint, so just left blank
63 | U1, U2, U5, U7, U9, U25, U28, U30, | 8 | Texas Instruments | TPD4E05U06DQAR | TVS DIODE 5.5V 14V 10SON | 10-UFDFN | SMD
64 | U3, | 1 | Diodes Incorporated | DMP3056LDM-7 | MOSFET P-CH 30V 4.3A SOT-26 | SOT-23-6 | SMD
65 | U4, | 1 | Toshiba Semiconductor and Storage | TC7USB40FT | IC SWITCH USB DUAL SPDT 14TSSOP | 14-TSSOP | SMD
66 | U6, | 1 | Toshiba Semiconductor and Storage | TB6612FNG | IC MOTOR DRIVER 2.7V-5.5V | 24-SSOP | SMD
67 | U8, | 1 | Richtek USA Inc. | RT9742CGJ5 | IC PWR SWTCH N-CHAN 1:1 | TSOT-23-5 | SMD
68 | U10, U20, | 2 | Diodes Incorporated | PI4ULS5V201TAEX | IC TRNSLTR BIDIRECTIONAL | SOT-23-6 | SMD
69 | U11, U14, | 2 | Diodes Incorporated | 74LVC1G126W5-7 | IC BUFFER NON-INVERT 5.5V | SOT-25 | SMD
70 | U12, | 1 | Diodes Incorporated | 74LVC1G07W5-7 | IC BUFFER NON-INVERT 5.5V | SOT-25 | SMD
71 | U13, U26, | 2 | ON Semiconductor | MC74VHC1G01DFT1G | IC GATE NAND 1CH 2-INP SC88A | 5-TSSOP, SC-70-5, SOT-353 | SMD
72 | U15, | 1 | Diodes Incorporated | AS78L05RTR-E1 | IC REG LINEAR 5V 100MA | SOT-89-3 | SMD
73 | U16, | 1 | Monolithic Power Systems Inc. | MP2619EV-LF-Z | IC BATT CHRG LI-ION | 28-VFQFN (4x5) Exposed Pad | SMD
74 | U17, | 1 | Diodes Incorporated | AP6503SP-13 | IC REG BUCK ADJUSTABLE 3A | 8-SOIC (0.154", 3.90mm Width) Exposed Pad | SMD
75 | U18, | 1 | GSTEK(Green Solution Technology) | GS9238 | TQFN23-4x4 DC-DC Converters RoHS | TQFN23-4x4 | SMD
76 | U19, | 1 | Diodes Incorporated | LMV331SE-7 | IC COMPARATOR TINY LV | SOT-353 | SMD
77 | U21, | 1 | Texas Instruments | TXB0102DCUR | IC TRNSLTR BIDIRECTIONAL US8 | 8-VFSOP (0.091", 2.30mm Width) | SMD
78 | U22, | 1 | Microchip Technology | AT24C02D-MAHM-T | IC EEPROM 2K I2C 1MHZ | 8-UFDFN Exposed Pad | SMD
79 | U23, | 1 | Nexperia USA Inc. | 74LVC4245APW,112 | IC TRNSLTR BIDIRECTIONAL | 24-TSSOP (0.173", 4.40mm Width) | SMD
80 | U24, | 1 | Texas Instruments | TLV70218DBVR | IC REG LINEAR 1.8V 300MA | SOT-23-5 | SMD
81 | U27, | 1 | Diodes Incorporated | DMP3056LSD-13 | MOSFET 2P-CH 30V 6.9A | 8-SOIC (0.154", 3.90mm Width) | SMD

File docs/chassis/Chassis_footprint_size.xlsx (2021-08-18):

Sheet: Chassis Footprint
Field | Value | Units | Equations | Notes
w | 53 | mm | (w+r1)^2 + (L/2)^2 = (r2)^2
L | 126.6950496 | mm | 2*sqrt(r2^2 - (w+r2)^2)
r1 (inner) | 53.4 | mm
r2 (outer) | 123.83 | mm

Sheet: Density Calcs
Field | Weight (lb) | Volume (mm³) | Density (lb/mm3) | Material | Comments
Fan | 0.0366 | 17600 | 2.079545455e-06
NanoHeat Sink + Nano Module | 0.138 | 54348.188 | 2.539183091e-06
A00 Baseboard | 0.078 | 7604.662 | 1.025686612e-05 |  | Approximated to just PCB
3S LiPo Battery | 0.3229 | 62997.818 | 5.125574349e-06
Wheel (32x7 mm) | 0.006875 | 3212.376 | 2.14016043e-06
Polulu Motors | 0.04299014 | 14495.798 | 2.96569668e-06
Wheel (40x7 mm) | 0.009375 | 4211.964 | 2.2258025e-06
Ball Caster | 0.0017637 | 853.008 | 2.067624219e-06

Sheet: v5 COM Calcs
Center of Mass / Tipping Calculations
Field | Value | Units | Equation | Notes
Width of Robot | 0.053 | m
Gravitational Force | 9.087 | m/s^2
Mass of Robot | 0.58 | kg |  | Pulled from "Total Weight of Robot" Sheet
Max Velocity | 0.5 | m/s
Inner length from Center of turn to middle of robot | 0.086787 | m |  | Measured by using onshape, using min robot width of 53 mm and constraining outer side to curve
Outer length from Center of turn to middle of robot | 0.165765 | m |  | Measured by using onshape, using min robot width of 53 mm and constraining outer side to curve
Distance from center of mass to outer edge of robot | 0.0265 | m |  | Approximated to be half of width of robot
Normal Force | 5.27046 | N | F_N = m*g
Normal Force from one wheel | 2.63523 | N | F_N = m*g/2 | Normal force from one wheel, approximated from dividing normal force by 2
Normal Force torque from one wheel | 0.069833595 | N*m | torque = r*F*sin(theta) | In this case F is the normal force from one wheel, r is the distance from the center of mass to outer edge of robot, and theta is 90 degrees
Calculated Min Height for Center of Mass using Inner radius | 0.04179757386 | m | t_com = t_n = (mv^2/r) * height
Calculated Min Height for Center of Mass using outer radius | 0.07983424742 | m | t_com = t_n = (mv^2/r) * height

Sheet: Horiz v6 COM Calcs
Center of Mass / Tipping Calculations
Field | Value | Units | Equation | Notes
Width of Robot | 0.053 | m
Gravitational Force | 9.087 | m/s^2
Mass of Robot | 0.507 | kg |  | Pulled from "Total Weight of Robot" Sheet
Max Velocity | 0.457 | m/s
Inner length from Center of turn to middle of robot | 0.079205 | m |  | Measured by using onshape, using min robot width of 53 mm and constraining outer side to curve
Outer length from Center of turn to middle of robot | 0.161398 | m |  | Measured by using onshape, using min robot width of 53 mm and constraining outer side to curve
Distance from center of mass to outer edge of robot | 0.0265 | m |  | Approximated to be half of width of robot
Normal Force | 4.607109 | N | F_N = m*g
Normal Force from one wheel | 2.3035545 | N | F_N = m*g/2 | Normal force from one wheel, approximated from dividing normal force by 2
Normal Force torque from one wheel | 0.06104419425 | N*m | torque = r*F*sin(theta) | In this case F is the normal force from one wheel, r is the distance from the center of mass to outer edge of robot, and theta is 90 degrees
Calculated Min Height for Center of Mass using Inner radius | 0.04566217609 | m | t_com = t_n = (mv^2/r) * height
Calculated Min Height for Center of Mass using outer radius | 0.0930469528 | m | t_com = t_n = (mv^2/r) * height

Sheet: Vert v6 COM Calcs
Center of Mass / Tipping Calculations |  |  |  |  | 0.455389
Field | Value | Units | Equation | Notes
Width of Robot | 0.053 | m
Gravitational Force | 9.087 | m/s^2
Mass of Robot | 0.455389 | kg |  | Pulled from "Total Weight of Robot" Sheet
Max Velocity | 0.46 | m/s
Inner length from Center of turn to middle of robot | 0.083875 | m |  | Measured by using onshape, using min robot width of 53 mm and constraining outer side to curve
Outer length from Center of turn to middle of robot | 0.164064 | m |  | Measured by using onshape, using min robot width of 53 mm and constraining outer side to curve
Distance from center of mass to outer edge of robot | 0.0265 | m |  | Approximated to be half of width of robot
Normal Force | 4.138119843 | N | F_N = m*g
Normal Force from one wheel | 2.069059922 | N | F_N = m*g/2 | Normal force from one wheel, approximated from dividing normal force by 2
Normal Force torque from one wheel | 0.05483008792 | N*m | torque = r*F*sin(theta) | In this case F is the normal force from one wheel, r is the distance from the center of mass to outer edge of robot, and theta is 90 degrees
Calculated Min Height for Center of Mass using Inner radius | 0.0477258065 | m | t_com = t_n = (mv^2/r) * height
Calculated Min Height for Center of Mass using outer radius | 0.09335423807 | m | t_com = t_n = (mv^2/r) * height

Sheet: Vert v7 COM Calcs
Center of Mass / Tipping Calculations
Field | Value | Units | Equation | Notes
Width of Robot | 0.048 | m
Gravitational Force | 9.087 | m/s^2
Mass of Robot | 0.464189 | kg |  | Pulled from "Total Weight of Robot" Sheet
Max Velocity | 0.435 | m/s
Inner length from Center of turn to middle of robot | 0.08208 | m |  | Measured by using onshape, using min robot width of 53 mm and constraining outer side to curve
Outer length from Center of turn to middle of robot | 0.164109 | m |  | Measured by using onshape, using min robot width of 53 mm and constraining outer side to curve
Distance from center of mass to outer edge of robot | 0.024 | m |  | Approximated to be half of width of robot
Normal Force | 4.218085443 | N | F_N = m*g
Normal Force from one wheel | 2.109042721 | N | F_N = m*g/2 | Normal force from one wheel, approximated from dividing normal force by 2
Normal Force torque from one wheel | 0.05061702532 | N*m | torque = r*F*sin(theta) | In this case F is the normal force from one wheel, r is the distance from the center of mass to outer edge of robot, and theta is 90 degrees
Calculated Min Height for Center of Mass using Inner radius | 0.04729994197 | m | t_com = t_n = (mv^2/r) * height
Calculated Min Height for Center of Mass using outer radius | 0.09457049436 | m | t_com = t_n = (mv^2/r) * height

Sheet: Jetbot Mini v5 Weight
Field | Count | Weight | Total | Units | Notes | Link
Jetbot Mini Chassis v5 | 1 | 134 | 134 | g | Layer: 0.25 mm, Infill: 20%, Support: on
Jetbot Mini Camera Mount | 1 | 3 | 3 | g | Layer: 0.25 mm, Infill: 20%, Support: on
GOLDBAT 1500 mAh 3S 11.1V 100C Battery | 1 | 146.25 | 146.25 | g | Average weight of the two batteries, note that website says 121.6 g | https://www.amazon.com/GOLDBAT-Softcase-m4-fpv250-Shredder-Helicopter/dp/B07ZFDJWR1
Jetson Nano module + Heat Sink + Noctua Fan | 1 | 81.1 | 81.1 | g | Jetson Nano module is 18 g? | https://forums.developer.nvidia.com/t/weight-of-jetson-modules/80396
A00 Basebord + Male Headers | 1 | 36.1 | 36.1 | g
Female XT60 Female Connector | 1 | 18.1 | 18.1 | g | Actual weight may be lower as the wires need to be trimmed, 7.72 g listed? | https://www.amazon.com/Female-Connector-Housing-Silicon-Battery/dp/B073QJWVVK?th=1
IMX219-160 8-Megapixels Camera Module 3280 × 2464 | 2 | 8.99 | 17.98 | g | Measured weight is 6.4 g, listed weight is 8.99 g | https://www.amazon.com/dp/B07T43K7LC//ref=cm_sw_su_dp
120:1 Mini Plastic Gearmotor, 90° 3mm D-Shaft Output, Extended Motor Shaft | 2 | 19.5 | 39 | g | Was not able to measure as do not have these motors on hand, used values from site | https://www.pololu.com/product/1515/specs
Pololu Wheel 60×8mm | 2 | 11.34 | 22.68 | g | Was not able to measure as do not have these wheels on hand, used values from site | https://www.pololu.com/product/1420
Pololu Ball Caster with 3/4″ Plastic Ball | 1 | 7 | 7 | g | Was not able to measure as do not have this part on hand, used value from site | https://www.pololu.com/product/954
M2.5 x 15 mm Standoffs | 4 | 1.4 | 5.6 | g |  | https://www.microcenter.com/product/622303/micro-connectors-assorted-m25-standoff-kit-114-pieces
Screws for standoffs | 4 | 0.25 | 1 | g |  | https://www.microcenter.com/product/622303/micro-connectors-assorted-m25-standoff-kit-114-pieces
Dev Kit Smaller Standoffs | 2 | 0.7 | 1.4 | g
Makerfocus OLED Display + Female and Male Headers | 1 | 2.9 | 2.9 | g |  | https://www.makerfocus.com/collections/oled/products/2pcs-i2c-oled-display-module-0-91-inch-i2c-ssd1306-oled-display-module-1
TP-Link USB Wifi Adapter (TL-WN725N) | 1 | 2 | 2 | g | Site says 0.07 oz, which is about 1.98 g, use the measured value of 2 g as it is larger for more leeway | https://www.amazon.com/TP-Link-wireless-network-Adapter-SoftAP/dp/B008IFXQFU
NTC 3950 100K Thermistor Sensor | 1 | 8.8 | 8.8 | g |  | https://www.amazon.com/GODSHARK-Thermistor-Wiring-Printer-Heatbed/dp/B07JGJKPT9?s=industrial | https://www.amazon.com/Anycubic-Thermistor-Wiring-Printer-Heatbed/dp/B01B41K7OM?s=industrial
 |  | Total Weight: | 526.91 | g
 |  | 10% Tolerance | 579.601 | g
 |  | 20% Tolerance | 632.292 | g

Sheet: Jetbot Mini v6 Horiz Weight
Field | Count | Weight | Total | Units | Notes | Link
Jetbot Mini Vert Chassis v6 | 1 | 92 | 92 | g | Layer: 0.25 mm, Infill: 30%, Support: on
Jetbot Mini Camera Mount | 1 | 2 | 2 | g | Layer: 0.22 mm, Infill: 30%, Support: on
GOLDBAT 1500 mAh 3S 11.1V 100C Battery | 1 | 146.25 | 146.25 | g | Average weight of the two batteries, note that website says 121.6 g | https://www.amazon.com/GOLDBAT-Softcase-m4-fpv250-Shredder-Helicopter/dp/B07ZFDJWR1
Jetson Nano module + Heat Sink + Noctua Fan | 1 | 81.1 | 81.1 | g | Jetson Nano module is 18 g? | https://forums.developer.nvidia.com/t/weight-of-jetson-modules/80396
A00 Basebord + Male Headers | 1 | 36.1 | 36.1 | g
Female XT60 Female Connector | 1 | 18.1 | 18.1 | g | Actual weight may be lower as the wires need to be trimmed, 7.72 g listed? | https://www.amazon.com/Female-Connector-Housing-Silicon-Battery/dp/B073QJWVVK?th=1
IMX219-160 8-Megapixels Camera Module 3280 × 2464 | 2 | 8.99 | 17.98 | g | Measured weight is 6.4 g, listed weight is 8.99 g | https://www.amazon.com/dp/B07T43K7LC//ref=cm_sw_su_dp
120:1 Mini Plastic Gearmotor, 90° 3mm D-Shaft Output, Extended Motor Shaft | 2 | 19.5 | 39 | g | Was not able to measure as do not have these motors on hand, used values from site | https://www.pololu.com/product/1515/specs
Pololu Wheel 40x7mm | 2 | 4.25 | 8.5 | g | Was not able to measure as do not have these wheels on hand, used values from site | https://www.pololu.com/product/1088/specs
Pololu Ball Caster with 3/8″ Plastic Ball | 1 | 0.8 | 0.8 | g | Was not able to measure as do not have this part on hand, used value from site | https://www.pololu.com/product/950/specs
M2.5 x 6 mm Standoffs | 4 | 0.6 | 2.4 | g |  | https://www.microcenter.com/product/622303/micro-connectors-assorted-m25-standoff-kit-114-pieces
Nut for Standoff | 4 | 0.23 | 0.92 | g |  | https://www.microcenter.com/product/622303/micro-connectors-assorted-m25-standoff-kit-114-pieces
Screws for standoffs | 4 | 0.25 | 1 | g |  | https://www.microcenter.com/product/622303/micro-connectors-assorted-m25-standoff-kit-114-pieces
Dev Kit Smaller Standoffs | 2 | 0.7 | 1.4 | g
Makerfocus OLED Display + Female and Male Headers | 1 | 2.9 | 2.9 | g |  | https://www.makerfocus.com/collections/oled/products/2pcs-i2c-oled-display-module-0-91-inch-i2c-ssd1306-oled-display-module-1
TP-Link USB Wifi Adapter (TL-WN725N) | 1 | 2 | 2 | g | Site says 0.07 oz, which is about 1.98 g, use the measured value of 2 g as it is larger for more leeway | https://www.amazon.com/TP-Link-wireless-network-Adapter-SoftAP/dp/B008IFXQFU
NTC 3950 100K Thermistor Sensor | 1 | 8.8 | 8.8 | g |  | https://www.amazon.com/GODSHARK-Thermistor-Wiring-Printer-Heatbed/dp/B07JGJKPT9?s=industrial | https://www.amazon.com/Anycubic-Thermistor-Wiring-Printer-Heatbed/dp/B01B41K7OM?s=industrial
 |  | Total Weight: | 461.25 | g
 |  | 10% Tolerance | 507.375 | g
 |  | 20% Tolerance | 553.5 | g

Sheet: Jetbot Mini v6 Vert Weight
Field | Count | Weight | Total | Units | Notes | Link
Jetbot Mini Vert Chassis v6 | 1 | 47 | 47 | g | Layer: 0.25 mm, Infill: 30%, Support: on
Jetbot Mini Camera Mount | 1 | 2 | 2 | g | Layer: 0.22 mm, Infill: 30%, Support: on
GOLDBAT 1500 mAh 3S 11.1V 100C Battery | 1 | 146.25 | 146.25 | g | Average weight of the two batteries, note that website says 121.6 g | https://www.amazon.com/GOLDBAT-Softcase-m4-fpv250-Shredder-Helicopter/dp/B07ZFDJWR1
Jetson Nano module + Heat Sink + Noctua Fan | 1 | 81.1 | 81.1 | g | Jetson Nano module is 18 g? | https://forums.developer.nvidia.com/t/weight-of-jetson-modules/80396
A00 Basebord + Male Headers | 1 | 36.1 | 36.1 | g
Female XT60 Female Connector | 1 | 18.1 | 18.1 | g | Actual weight may be lower as the wires need to be trimmed, 7.72 g listed? | https://www.amazon.com/Female-Connector-Housing-Silicon-Battery/dp/B073QJWVVK?th=1
IMX219-160 8-Megapixels Camera Module 3280 × 2464 | 2 | 8.99 | 17.98 | g | Measured weight is 6.4 g, listed weight is 8.99 g | https://www.amazon.com/dp/B07T43K7LC//ref=cm_sw_su_dp
120:1 Mini Plastic Gearmotor, 90° 3mm D-Shaft Output, Extended Motor Shaft | 2 | 19.5 | 39 | g | Was not able to measure as do not have these motors on hand, used values from site | https://www.pololu.com/product/1515/specs
Pololu Wheel 32×7mm | 2 | 3.12 | 6.24 | g | Was not able to measure as do not have these wheels on hand, used values from site | https://www.pololu.com/product/1088/specs
Pololu Ball Caster with 3/8″ Plastic Ball | 1 | 0.8 | 0.8 | g | Was not able to measure as do not have this part on hand, used value from site | https://www.pololu.com/product/950/specs
M2.5 x 6 mm Standoffs | 4 | 0.6 | 2.4 | g |  | https://www.microcenter.com/product/622303/micro-connectors-assorted-m25-standoff-kit-114-pieces
Nut for Standoff | 4 | 0.23 | 0.92 | g |  | https://www.microcenter.com/product/622303/micro-connectors-assorted-m25-standoff-kit-114-pieces
Screws for standoffs | 4 | 0.25 | 1 | g |  | https://www.microcenter.com/product/622303/micro-connectors-assorted-m25-standoff-kit-114-pieces
Dev Kit Smaller Standoffs | 2 | 0.7 | 1.4 | g
Makerfocus OLED Display + Female and Male Headers | 1 | 2.9 | 2.9 | g |  | https://www.makerfocus.com/collections/oled/products/2pcs-i2c-oled-display-module-0-91-inch-i2c-ssd1306-oled-display-module-1
TP-Link USB Wifi Adapter (TL-WN725N) | 1 | 2 | 2 | g | Site says 0.07 oz, which is about 1.98 g, use the measured value of 2 g as it is larger for more leeway | https://www.amazon.com/TP-Link-wireless-network-Adapter-SoftAP/dp/B008IFXQFU
NTC 3950 100K Thermistor Sensor | 1 | 8.8 | 8.8 | g |  | https://www.amazon.com/GODSHARK-Thermistor-Wiring-Printer-Heatbed/dp/B07JGJKPT9?s=industrial | https://www.amazon.com/Anycubic-Thermistor-Wiring-Printer-Heatbed/dp/B01B41K7OM?s=industrial
 |  | Total Weight: | 413.99 | g
 |  | 10% Tolerance | 455.389 | g
 |  | 20% Tolerance | 496.788 | g

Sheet: Jetbot Mini v7 Vert Weight
Field | Count | Weight | Total | Units | Notes | Link
Jetbot Mini Vert Chassis v6 | 1 | 55 | 55 | g | Layer: 0.25 mm, Infill: 30%, Support: on
Jetbot Mini Camera Mount | 1 | 2 | 2 | g | Layer: 0.22 mm, Infill: 30%, Support: on
GOLDBAT 1500 mAh 3S 11.1V 100C Battery | 1 | 146.25 | 146.25 | g | Average weight of the two batteries, note that website says 121.6 g | https://www.amazon.com/GOLDBAT-Softcase-m4-fpv250-Shredder-Helicopter/dp/B07ZFDJWR1
Jetson Nano module + Heat Sink + Noctua Fan | 1 | 81.1 | 81.1 | g | Jetson Nano module is 18 g? | https://forums.developer.nvidia.com/t/weight-of-jetson-modules/80396
A00 Basebord + Male Headers | 1 | 36.1 | 36.1 | g
Female XT60 Female Connector | 1 | 18.1 | 18.1 | g | Actual weight may be lower as the wires need to be trimmed, 7.72 g listed? | https://www.amazon.com/Female-Connector-Housing-Silicon-Battery/dp/B073QJWVVK?th=1
IMX219-160 8-Megapixels Camera Module 3280 × 2464 | 2 | 8.99 | 17.98 | g | Measured weight is 6.4 g, listed weight is 8.99 g | https://www.amazon.com/dp/B07T43K7LC//ref=cm_sw_su_dp
120:1 Mini Plastic Gearmotor, 90° 3mm D-Shaft Output, Extended Motor Shaft | 2 | 19.5 | 39 | g | Was not able to measure as do not have these motors on hand, used values from site | https://www.pololu.com/product/1515/specs
Pololu Wheel 32×7mm | 2 | 3.12 | 6.24 | g | Was not able to measure as do not have these wheels on hand, used values from site | https://www.pololu.com/product/1088/specs
Pololu Ball Caster with 3/8″ Plastic Ball | 1 | 0.8 | 0.8 | g | Was not able to measure as do not have this part on hand, used value from site | https://www.pololu.com/product/950/specs
M2.5 x 6 mm Standoffs | 4 | 0.6 | 2.4 | g |  | https://www.microcenter.com/product/622303/micro-connectors-assorted-m25-standoff-kit-114-pieces
Nut for Standoff | 4 | 0.23 | 0.92 | g |  | https://www.microcenter.com/product/622303/micro-connectors-assorted-m25-standoff-kit-114-pieces
Screws for standoffs | 4 | 0.25 | 1 | g |  | https://www.microcenter.com/product/622303/micro-connectors-assorted-m25-standoff-kit-114-pieces
Dev Kit Smaller Standoffs | 2 | 0.7 | 1.4 | g
Makerfocus OLED Display + Female and Male Headers | 1 | 2.9 | 2.9 | g |  | https://www.makerfocus.com/collections/oled/products/2pcs-i2c-oled-display-module-0-91-inch-i2c-ssd1306-oled-display-module-1
TP-Link USB Wifi Adapter (TL-WN725N) | 1 | 2 | 2 | g | Site says 0.07 oz, which is about 1.98 g, use the measured value of 2 g as it is larger for more leeway | https://www.amazon.com/TP-Link-wireless-network-Adapter-SoftAP/dp/B008IFXQFU
NTC 3950 100K Thermistor Sensor | 1 | 8.8 | 8.8 | g |  | https://www.amazon.com/GODSHARK-Thermistor-Wiring-Printer-Heatbed/dp/B07JGJKPT9?s=industrial | https://www.amazon.com/Anycubic-Thermistor-Wiring-Printer-Heatbed/dp/B01B41K7OM?s=industrial
 |  | Total Weight: | 421.99 | g
 |  | 10% Tolerance | 464.189 | g
 |  | 20% Tolerance | 506.388 | g

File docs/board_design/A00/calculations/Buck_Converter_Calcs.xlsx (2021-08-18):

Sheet: GS9238
GS9238 for 5V Buck Converter
Field | Value | Unit | Equation | Notes
Input Voltage Max | 20 | V
Input Voltage | 19 | V
Input Voltage Min | 12 | V
Output Voltage | 5 | V
Efficiency | 0.9
Output Current Max | 4.48 | A
Fsw | 350000 | Hz
Max Duty Cycle | 0.2777777778
Inductor Ripple Current | 1.659259259 | A
Max Switching Current | 5.30962963 | A
Inductance | 7.174744898 | uH | (3/(Iout * fsw)) * (((Vin_max - Vout) * Vout)/(Vin_max)) | From GS9238 Datasheet
Inductance (Ripple est. 20% of Max Output) | 11.95790816 | uH | Vout*(Vin_max - Vout) / (Iripple * fsw * Vin_max) | From TI: Basic Calculation of a Buck Converter's Power Stage
Inductance (Ripple est. 50% of Max Output) | 4.783163265 | uH | Vout*(Vin_max - Vout) / (Iripple * fsw * Vin_max) | From TI: Basic Calculation of a Buck Converter's Power Stage

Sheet: GS9238 Old Design
Field | Value | Units | Equations | Notes
Input Voltage Max | 20 | V
Input Voltage | 12 | V
Input Voltage Min | 10 | V
Output Voltage | 5 | V
Efficiency | 0.9 |  |  |  | 1000000000
Output Current Max | 4.48 | A
Rton | 1300000 | Ω
Ton Calculated Vmax | 1050 | ns | 100ns
Ton Calculated Vtyp | 1800 | ns
Ton Calculated Vin | 2191.304348 | ns
Fsw Calculated Vmax | 238.0952381 | KHz
Fsw Calculated Vtyp | 231.4814815 | KHz
Fsw Calculated Vin | 228.1746032 | KHz

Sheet: ESL Calcs
Field | Value | Unit | Equation | Note | Links | Can also use DF = ESR / Xc = tan(delta)
MPN | CL21A226MAYNNNE |  |  |  | http://weblib.samsungsem.com/mlcc/mlcc-ec-data-sheet.do?partNumber=CL21A226MAYNNN
Fsw | 98080 | Hz
ESR | 0.003911 | Ω
Z | 0.1144 | Ω
C | 2.2e-05 | F
ESL | 3.052186503e-07 | L | R^2 + (-1/wC + jL)^2 = Z^2
MPN | CL10A226MP8NUNE |  |  |  | http://weblib.samsungsem.com/mlcc/mlcc-ec-data-sheet.do?partNumber=CL10A226MP8NUN
Fsw | 324990 | Hz |  | Should be around 330 KHz, as this is target Fsw of Buck Converter
ESR | 0.00302 | Ω
Z | 0.03334 | Ω
C | 2.2e-05 | F
ESL | 2.716151176e-08 | L | R^2 + (-1/wC + jL)^2 = Z^2
MPN | CL10A226MP8NUNE |  |  | Values taken for 10uF / 6.3V | https://www.yageo.com/en/Chart/Index/CC0805MKX5R5BB476
Fsw | 340000 | Hz |  | Should be around 340 KHz
ESR | 0.003 | Ω
Z | 0.01 | Ω
C | 4.7e-05 | F
ESL | 9.127547923e-09 | L | R^2 + (-1/wC + jL)^2 = Z^2
MPN | CL10A226MP8NUNE |  |  | Values taken for 10uF / 6.3V
Fsw | 340000 | Hz |  | Should be around 340 KHz
ESR | 0.003 | Ω
Z | 0.01 | Ω
C | 4.7e-05 | F
ESL | 9.127547923e-09 | L | R^2 + (-1/wC + jL)^2 = Z^2
MPN | CL05A104KA5NNN |  |  | Values taken for 10uF / 6.3V
Fsw | 98080 | Hz |  | Should be around 340 KHz
ESR | 0.257 | Ω
Z | 18.52 | Ω
C | 1e-07 | F
ESL | 5.638133712e-05 | L | R^2 + (-1/wC + jL)^2 = Z^2

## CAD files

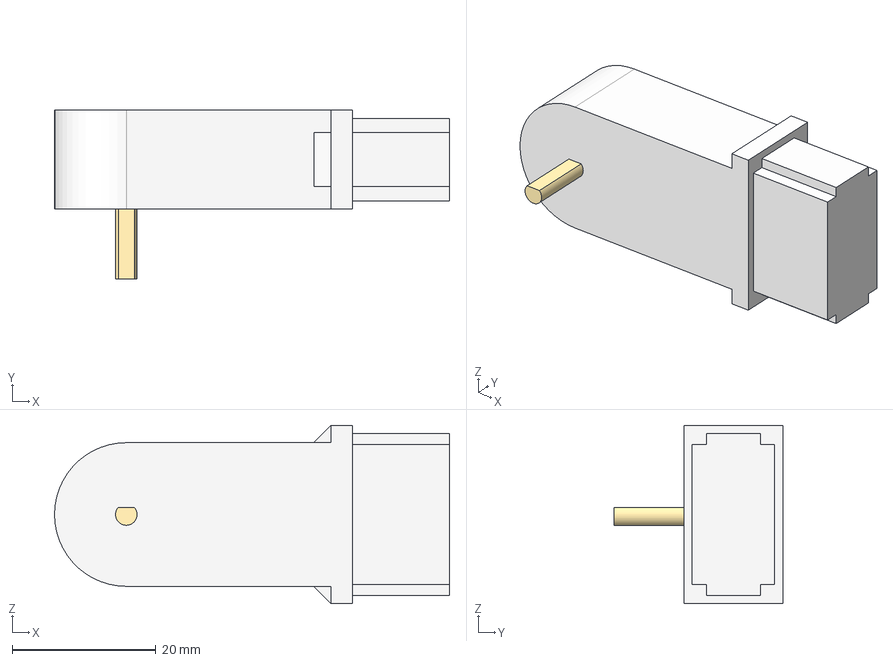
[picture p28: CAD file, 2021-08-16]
assets/chassis/general/general_step/Polulu_Mini_Plastic_Gearmotor_90°_3mm_D-Shaft_Output.step
55.0 x 23.5 x 24.8 mm

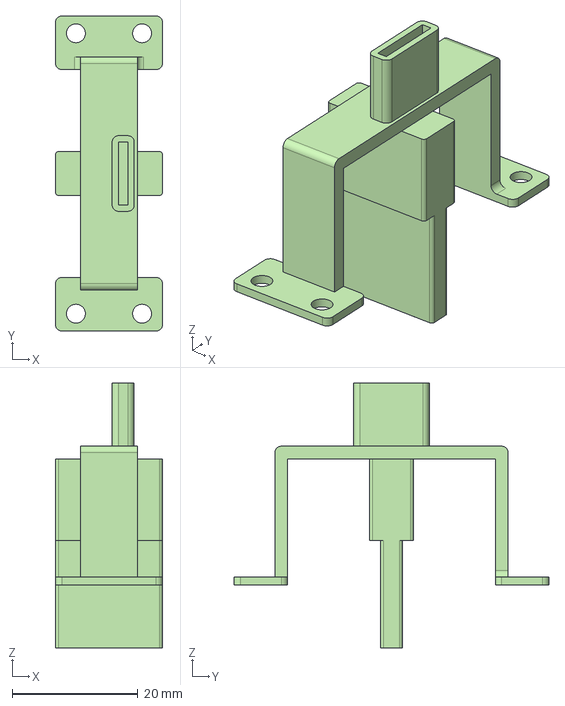
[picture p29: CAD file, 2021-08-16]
assets/chassis/v9/v9_step/Motor_Latch_v2.step
17.0 x 50.0 x 42.0 mm

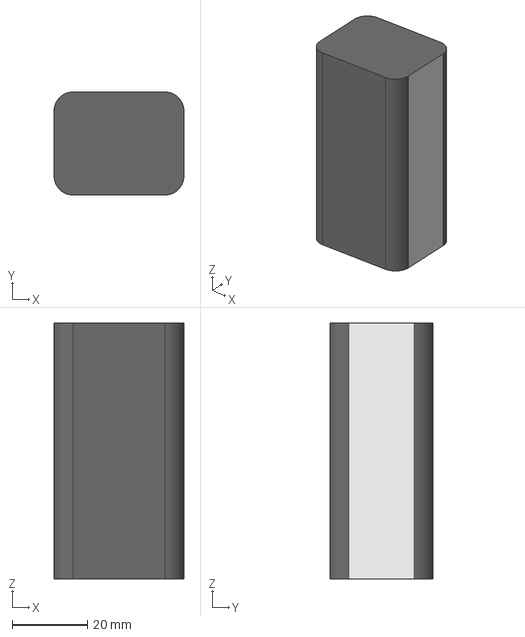
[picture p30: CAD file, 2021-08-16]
assets/chassis/general/general_step/HOOVO_3S_Lipo_Battery.step
34.5 x 27.4 x 68.1 mm

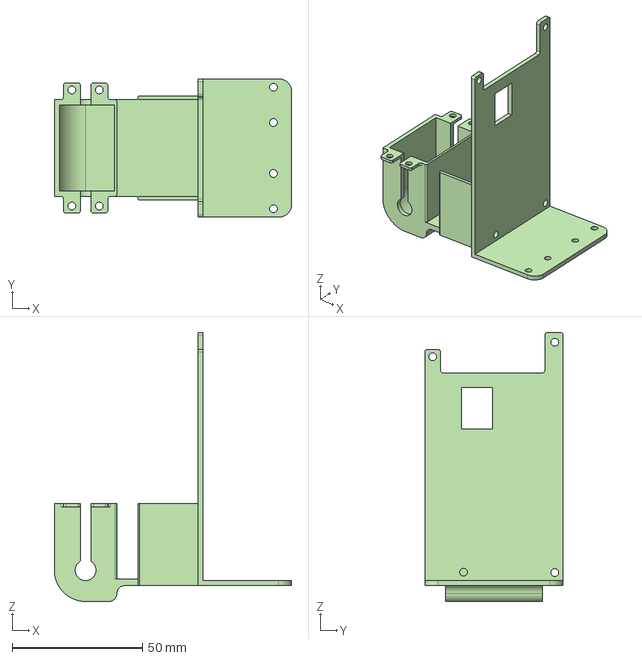
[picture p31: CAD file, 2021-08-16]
assets/chassis/v9/v9_step/Chassis_Body_v9_Vertical.step
91.0 x 53.0 x 103.1 mm

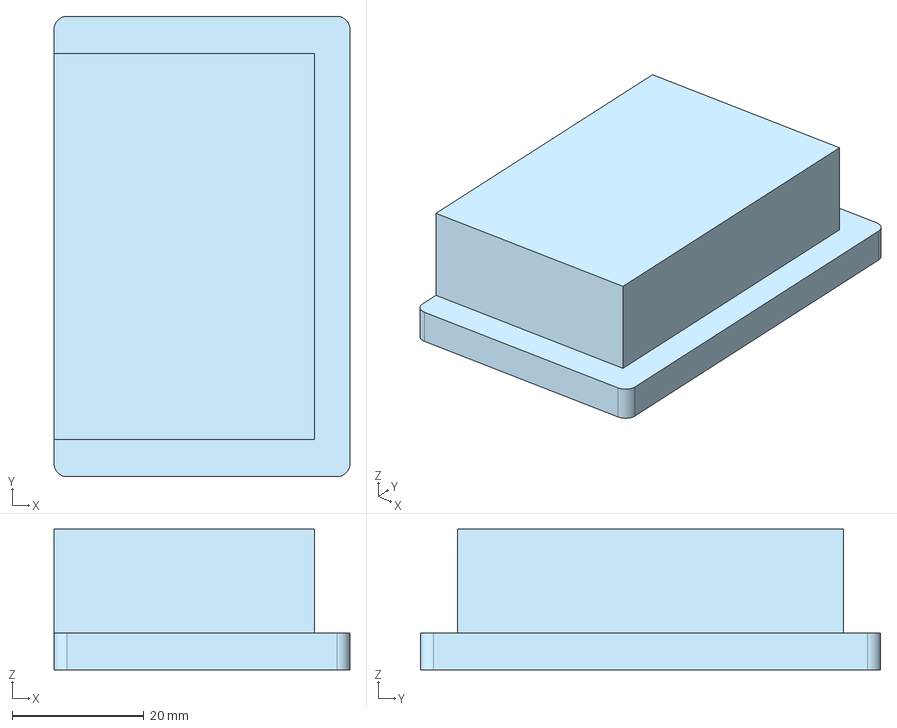
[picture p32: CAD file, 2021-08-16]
assets/chassis/general/general_step/Jetson_Nano_Module_Heat_Sink.step
45.0 x 70.0 x 21.4 mm

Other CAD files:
assets/chassis/general/general_iges/HOOVO_3S_Lipo_Battery.iges
assets/chassis/general/general_iges/Jetson_Nano_Module_Heat_Sink.iges
assets/chassis/general/general_iges/Polulu_Mini_Plastic_Gearmotor_90°_3mm_D-Shaft_Output.iges
assets/chassis/general/general_stl/HOOVO_3S_Lipo_Battery.stl
assets/chassis/general/general_stl/Jetson_Nano_Module_Heat_Sink.stl
assets/chassis/general/general_stl/Polulu_Mini_Plastic_Gearmotor_90°_3mm_D-Shaft_Output.stl
assets/chassis/v9/v9_iges/Chassis_Body_v9_Vertical.iges
assets/chassis/v9/v9_iges/Motor_Latch_v2.iges
assets/chassis/v9/v9_stl/Chassis_Body_v9_Vertical.stl
assets/chassis/v9/v9_stl/Motor_Latch_v2.stl

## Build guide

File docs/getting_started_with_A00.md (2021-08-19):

# Getting Started with A00

**A00 IS NOT RECOMMENDED FOR MANUFACTURE; this documentation is more to show how I setup the A00 Jetbot Minis and as a reference for A01.**

To get setup with the Jetbot Mini, please step through the [hardware](https://github.com/NVIDIA-AI-IOT/jetbot_mini/blob/main/docs/A00_hardware_setup.md) and [software](https://github.com/NVIDIA-AI-IOT/jetbot_mini/blob/main/docs/A00_software_setup.md) setup guides. 

For a brief overview of the project, refer to [this](https://github.com/NVIDIA-AI-IOT/jetbot_mini/blob/main/docs/project_overview.md) documentation. 

If you would like to learn more about the design of the Jetbot Mini, I recommend checking out the [board design](https://github.com/NVIDIA-AI-IOT/jetbot_mini/tree/main/docs/board_design), [chassis](https://github.com/NVIDIA-AI-IOT/jetbot_mini/tree/main/docs/chassis) and [software](https://github.com/NVIDIA-AI-IOT/jetbot_mini/tree/main/docs/software) documentation.

The KiCAD design files are located [here](https://github.com/NVIDIA-AI-IOT/jetbot_mini/tree/main/design).

The Onshape chassis design files are located [here](https://github.com/NVIDIA-AI-IOT/jetbot_mini/tree/main/assets/chassis). 

The software files are located [here](https://github.com/NVIDIA-AI-IOT/jetbot_mini/tree/main/jetbot). 

Happy Jetbot Mini'ing!

<p align="left">

</p>

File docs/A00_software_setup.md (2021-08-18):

# A00 Software Setup

**A00 IS NOT RECOMMENDED FOR MANUFACTURE; this documentation is more to show how I setup the A00 Jetbot Minis and as a reference for A01.**

To setup software, go through the following steps:

> MAKE SURE THAT THE JETSON NANO MODULE AND DEV KIT YOU ARE USING ARE B01 AND NOT A02. This is because the A00 baseboard CSI camera lanes are using the B01 dev kit setup. 

1. Do the A00 baseboard reworks. 
2. Flash SD card with [Jetpack 4.4](https://developer.nvidia.com/jetpack-sdk-44-archive).
> I used an older version of L4T and Jetpack because the Jetbot docker is designed to work with this version. I used a Jetson Nano image instead of the Jetbot image because I needed the [jetson-io tool](https://docs.nvidia.com/jetson/l4t/index.html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) to change two of the GPIOs to PWM, and the jetson-io tool does not work on the Jetbot image. 
3. Refer to [this tutorial](https://developer.nvidia.com/embedded/learn/get-started-jetson-nano-devkit) and prep your B01 Jetson Nano Module with the B01 dev kit. 
4. Step through the following [docker tutorial](https://jetbot.org/master/software_setup/docker.html) to setup the Jetbot repository onto the Jetson Nano image.
> Refer to the following [forum post](https://github.com/NVIDIA-AI-IOT/jetbot/issues/406) if you are having issues with the docker.  
5. Use the jetson-io tool to change GPIO33 and GPIO32 to PWM. 
6. Clone the [jetson-gpio](https://github.com/NVIDIA/jetson-gpio) and [Adafruit MotorHAT](https://github.com/adafruit/Adafruit-Motor-HAT-Python-Library) libraries in the notebooks folder of the Jetbot repository.  
7. Go to the [software folder](https://github.com/NVIDIA-AI-IOT/jetbot_mini/tree/main/jetbot) from this repo and replace all the corresponding files in your Jetson Nano module image with the ones in the folder. 
8. Connect your Jetson Nano module to the A00 baseboard. In order to connect to wifi, you need to first login to a serial terminal over UART.
9. Log into Jupyter Notebook, open up a terminal in Jupyter Notebook, and run "python3 setup.py install" for the jetbot, jetson-gpio, and Arduino MotorHAT libraries to add them to the Jupyter Notebook python modules. 
10. Your Jetbot Mini is now ready to step through the Jetbot examples!

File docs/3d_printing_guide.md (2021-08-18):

# 3D Printing Guide

I personally like using Cura to slice and prep stl files for printing. 
I used the Ender 3 to print out the necessary chassis files. 
Once Cura is downloaded, go through the following steps to print: 

1. Open Cura, click on the upper left folder icon and choose the stl file that you want to print. 
<p align="left">
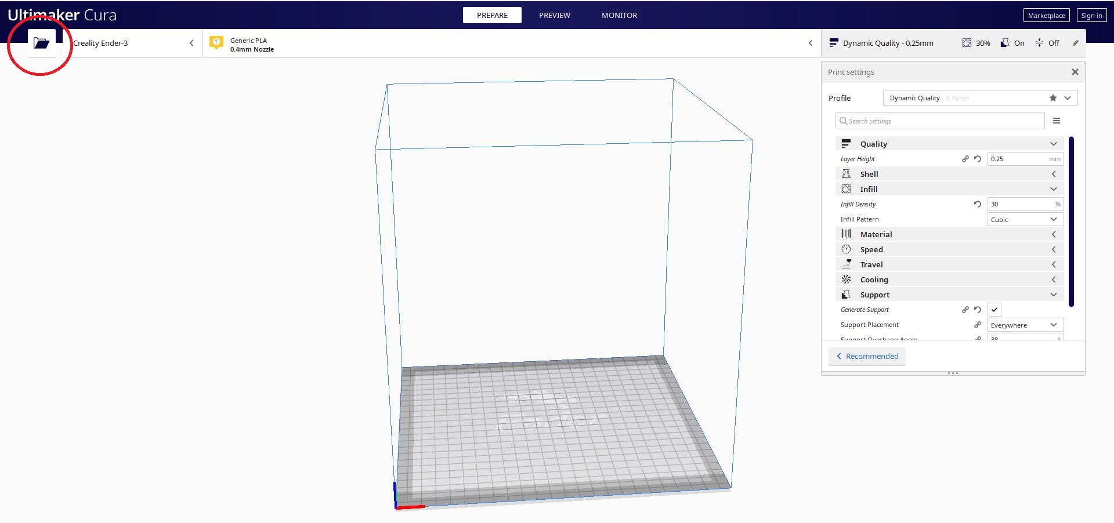
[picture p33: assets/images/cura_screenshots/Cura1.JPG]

</p>

2. Change the printer to match your printer; in my case its the Ender 3. 
<p align="left">
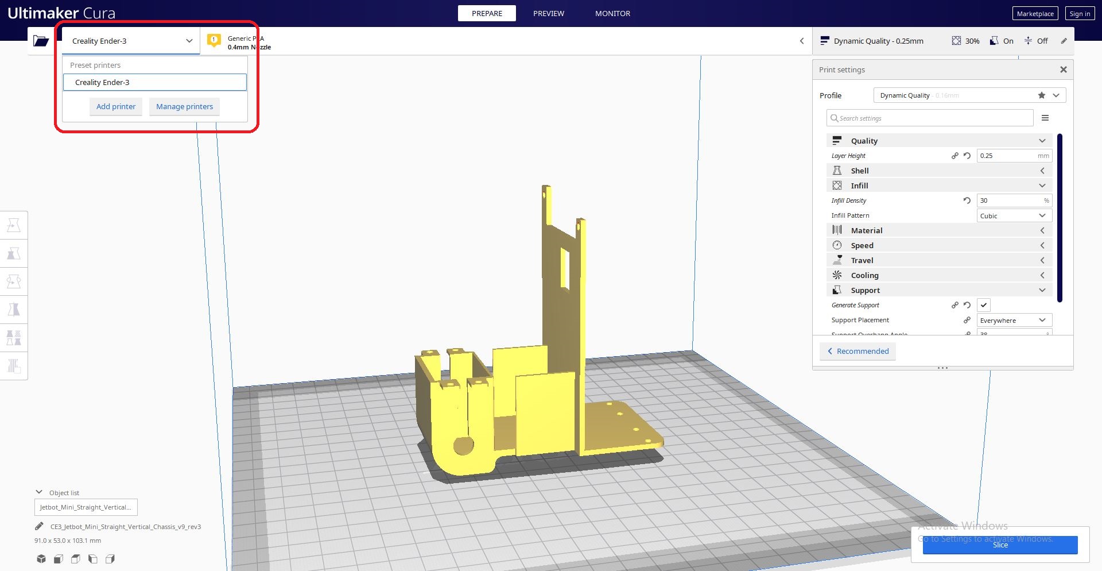
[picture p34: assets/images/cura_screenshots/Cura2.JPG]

</p>

3. Change the print settings; I like to use 0.25 mm layer height, 30% infill density, and enable support. Then click "Slice" on the lower right. 
<p align="left">
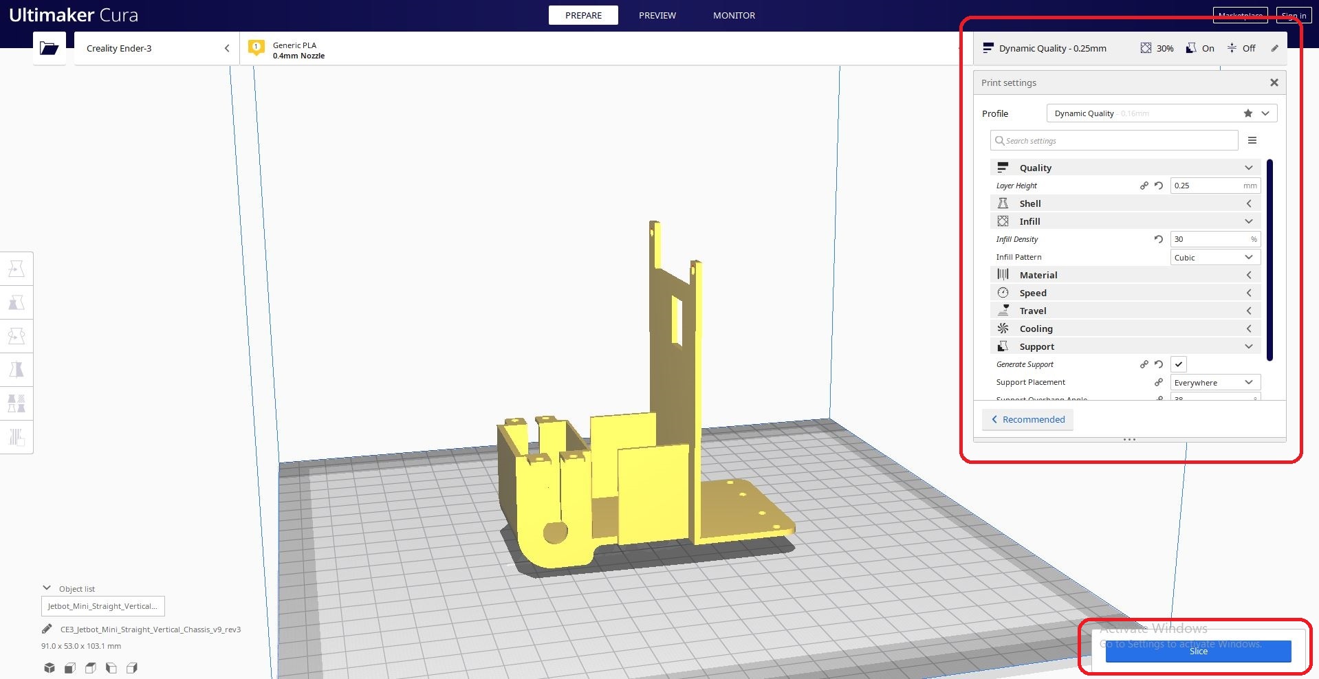
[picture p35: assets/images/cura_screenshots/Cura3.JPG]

</p>

4. Plug in a micro-sd card and save the sliced stl file to the sd card. This dialogue box shows you printing time and the amount of filament used. 
<p align="left">
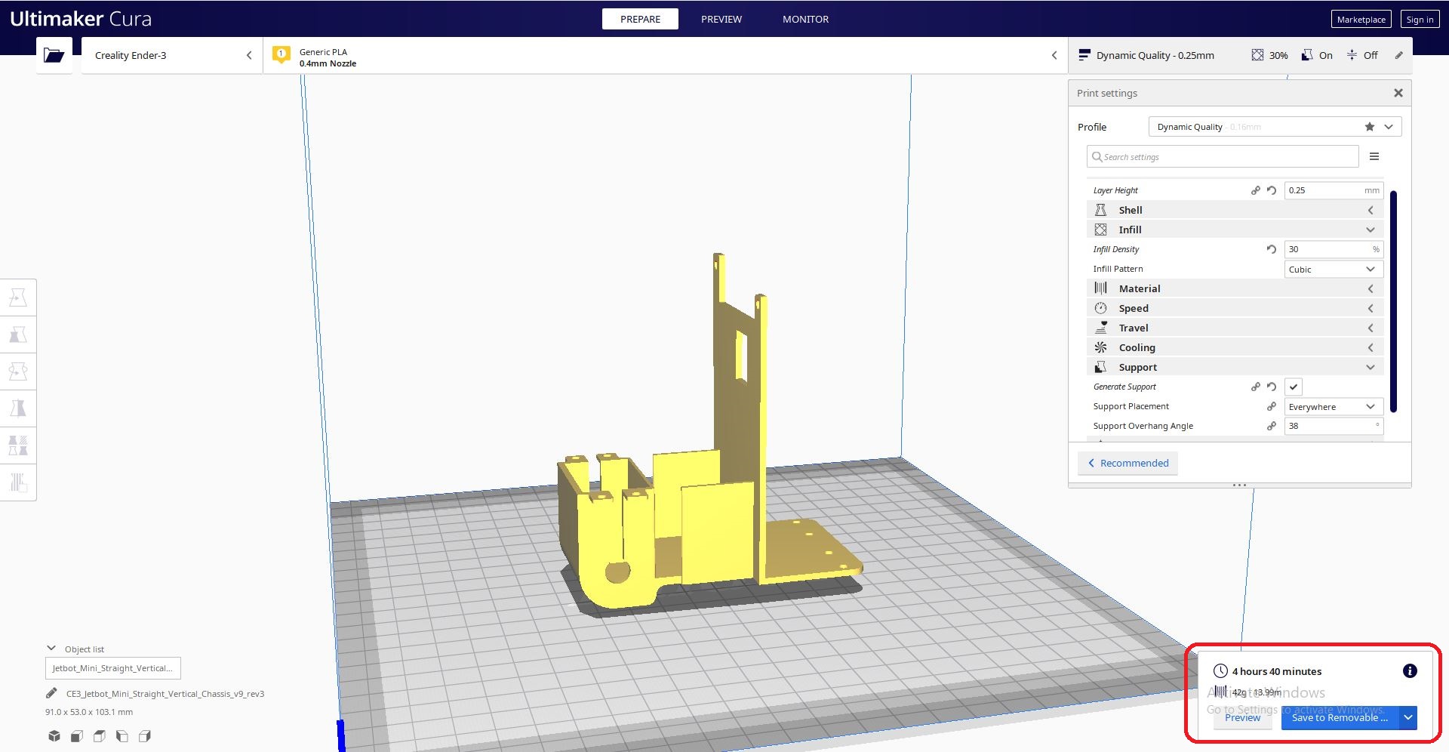
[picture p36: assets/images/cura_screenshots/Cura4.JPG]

</p>

5. You can check what will be printed by clicking "preview" at the top. 
<p align="left">
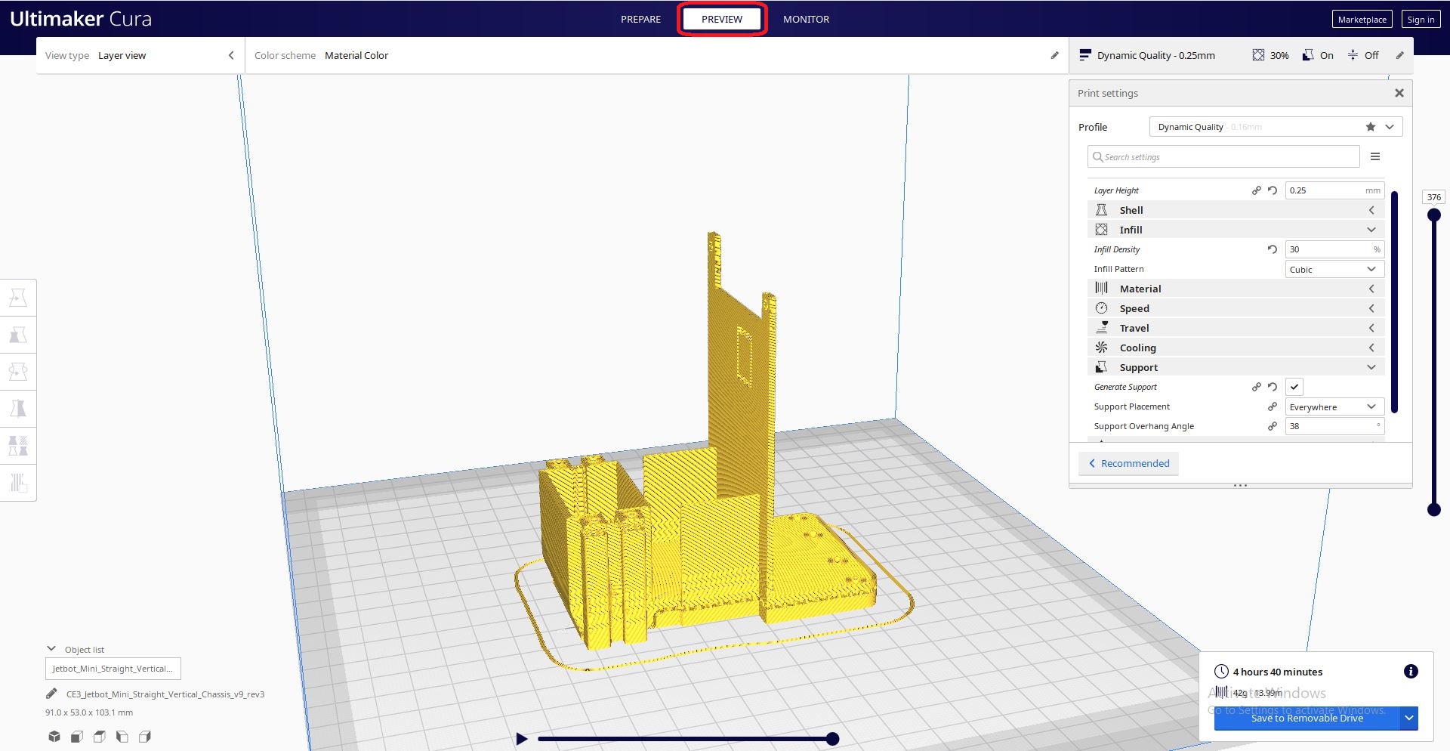
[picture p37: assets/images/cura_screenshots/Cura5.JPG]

</p>

6. Eject the micro-sd card, place it in your printer, and print!

## Do the following steps if you need to change the orientation of an stl file

1. Click on the CAD file that you need to change the orientation of. 
<p align="left">
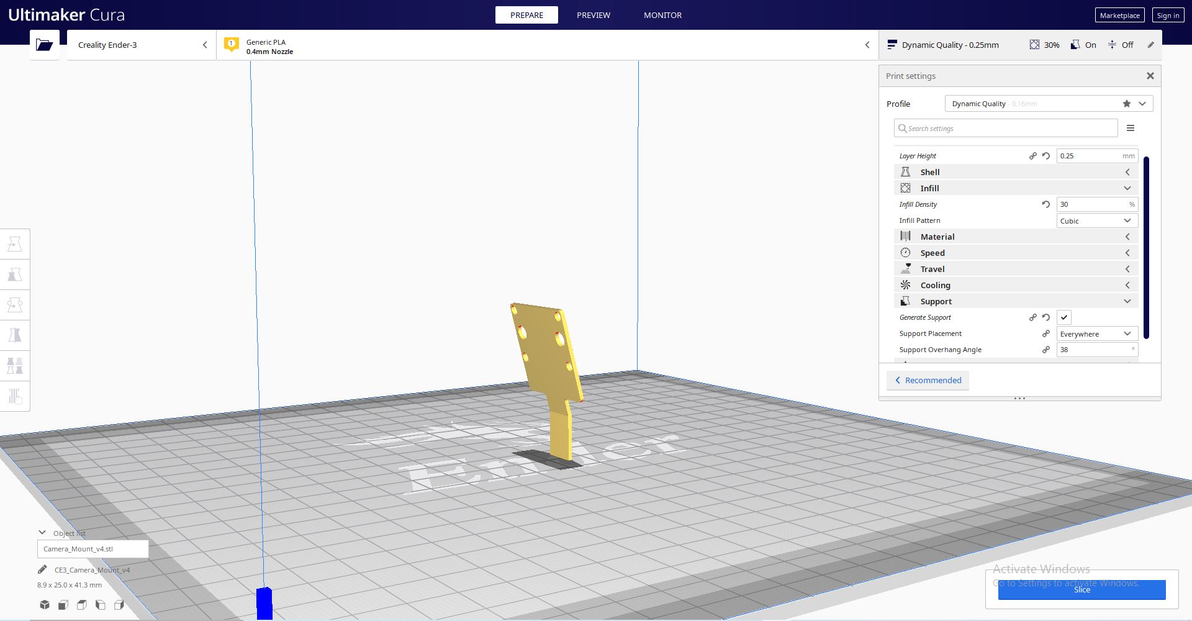
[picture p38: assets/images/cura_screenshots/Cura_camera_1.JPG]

</p>

2. Click on the third icon on the left ribbon and drag the corresponding circle in the direction you want to orient the CAD. In this case I dragged the green circle to the right. 
<p align="left">
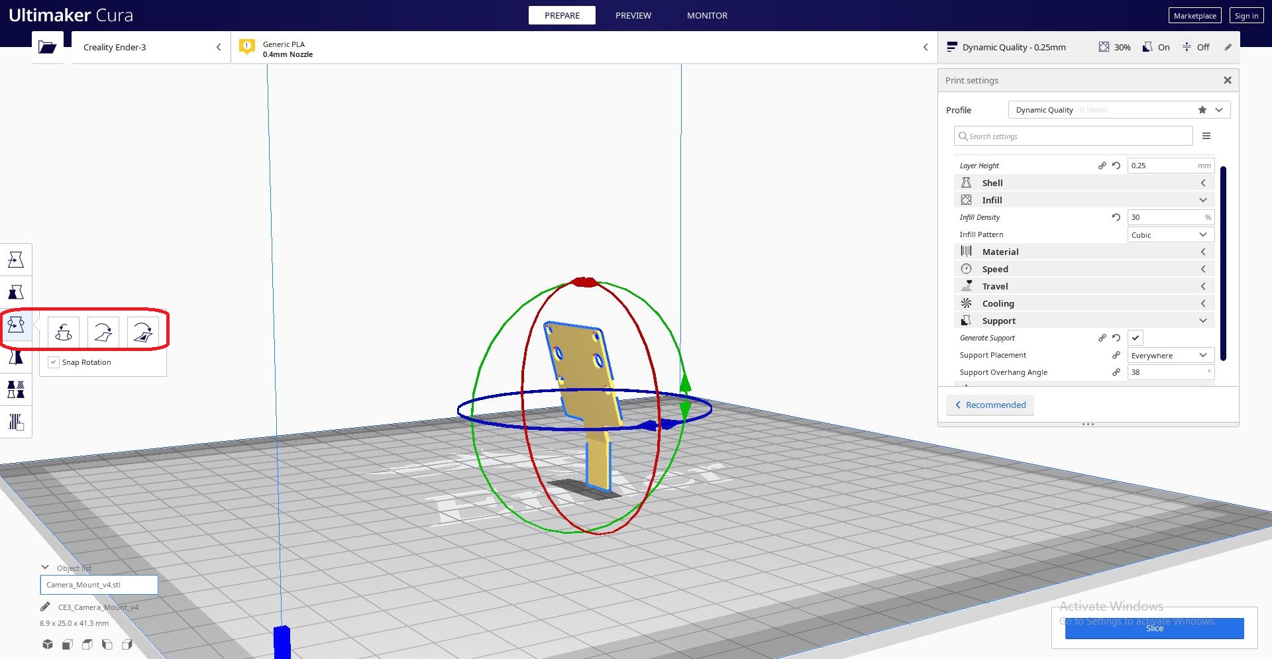
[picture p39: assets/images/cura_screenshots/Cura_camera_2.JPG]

</p>

3. Proceed with steps 3, 4, and 5. 
<p align="left">
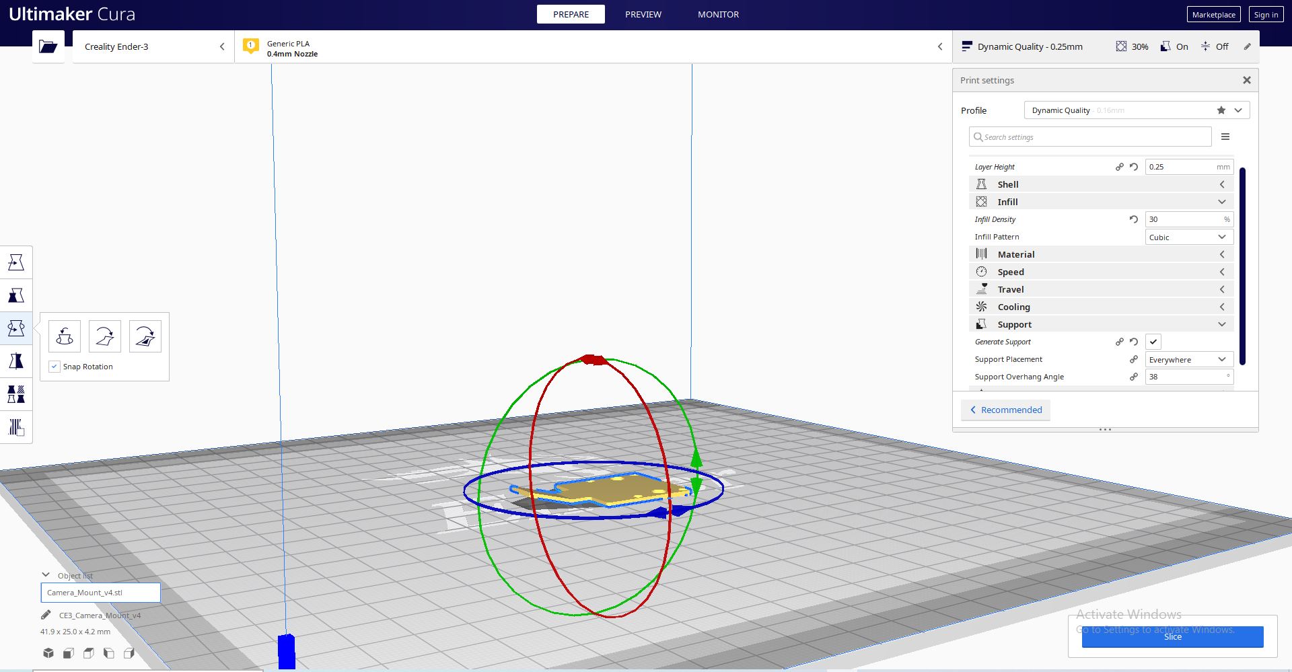
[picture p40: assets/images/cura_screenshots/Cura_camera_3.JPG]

</p>

## Happy 3D Printing!

https://user-images.githubusercontent.com/46247601/129833055-a0635bae-7684-466b-96b3-dfa1de1ba009.mp4

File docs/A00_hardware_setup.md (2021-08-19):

# A00 Hardware Setup

**A00 IS NOT RECOMMENDED FOR MANUFACTURE; this documentation is more to show how I setup the A00 Jetbot Minis and as a reference for A01.**

https://user-images.githubusercontent.com/46247601/129833388-8e8ddddb-3706-4f1e-b912-3f34c6a43b9e.mp4

**Please note that this page is still being worked on.**

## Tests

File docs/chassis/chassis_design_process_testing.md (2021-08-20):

# Chassis Design Process

The chassis was designed with Onshape, as it is an easy to learn cloud-based CAD program that is popular among makers. 
The main design goal of the chassis was that it had to be small enough to achive two-way traffic on the LEGO test roads. The main limiting factor is making sure two robots can make the turn at the same time. The following image shows the dimensions of the LEGO road turns that I tested the Jetbot Minis on. 

<p align="left">
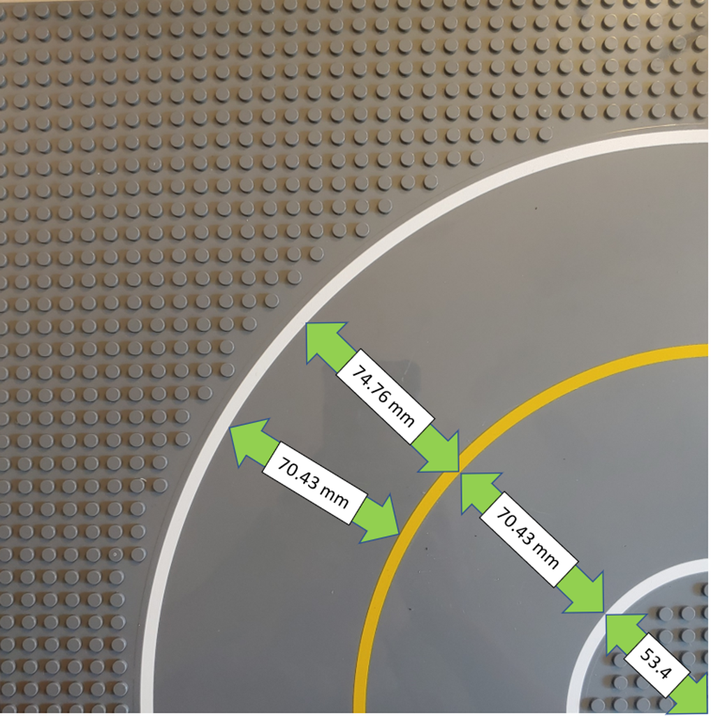
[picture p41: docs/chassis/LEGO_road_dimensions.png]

</p>

In order to hit the two-way traffic spec, I did some calculations with the help of Eric Nguyen, Lauren Sibley and Max Camposano show below: 

<p align="left">
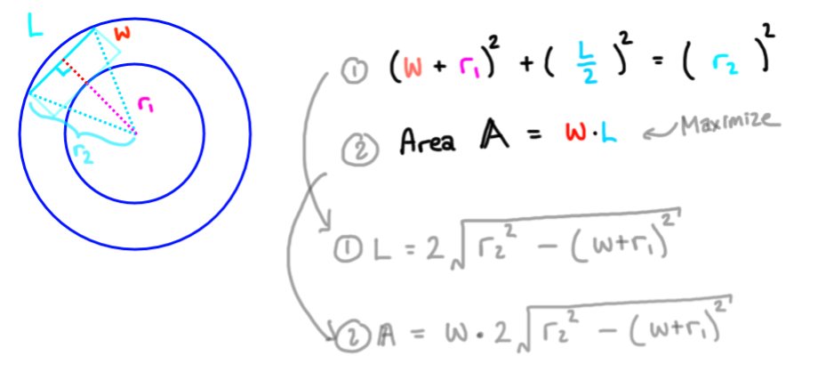
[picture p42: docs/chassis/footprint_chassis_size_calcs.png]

</p>

This calculation was done with the help of Eric Nguyen and puts a constraint on the width and length of the chassis. If a chassis' width and length satisfy the first equation, then theoretically it should be be able to make the turn. This assumes perfect motion and so is not an exact calculation, but it is a good approximation for whether the designed chassis will be able to hit the target specification.  

<p align="left">
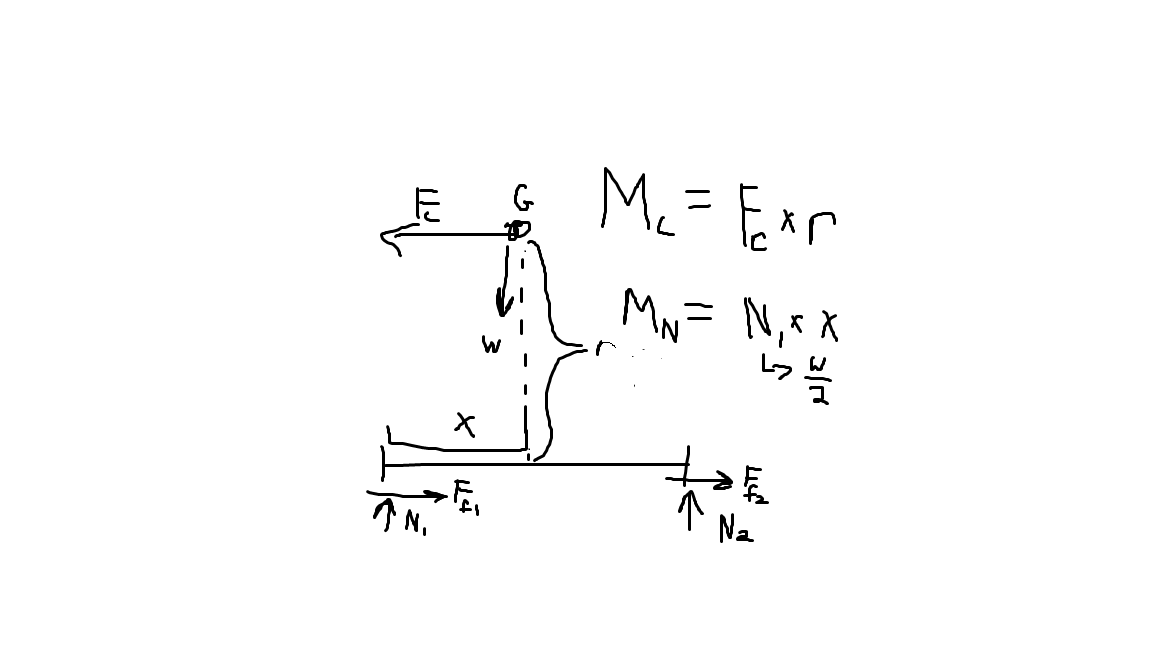
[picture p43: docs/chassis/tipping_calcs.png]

</p>

This calculation was done with the help of Lauren Sibley and Max Camposano. This is a stability calculation; notice that there is centripetal force acting on the center of gravity and normal force acting on the outer wheel. If the work done by the centripetal force exceeds the work done by the normal force, then the robot will tip. 

The following video shows how I confirmed the footprint size calculation; I would design a chassis, create a rectangle with its width and length specifications, constrain the rectangle to the inner curve of the LEGO turn in CAD, and try to drag the rectangle back and forth. Again, this test assumes perfect movement and so is not exact, but it is a good indicator of whether the designed chassis is in the right ball park. 

https://user-images.githubusercontent.com/46247601/129981877-6a9636c1-f6d4-4062-8df9-e6650edf48f4.mp4

The following image shows the timeline of different chassis that I considered for the Jetbot Mini.

<p align="left">
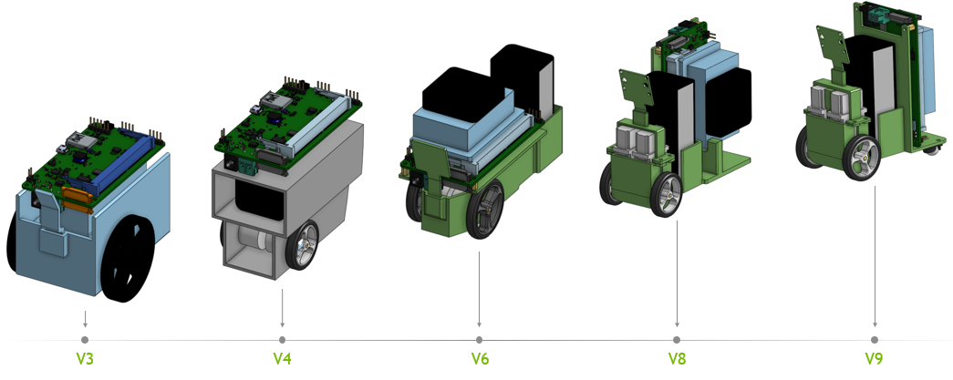
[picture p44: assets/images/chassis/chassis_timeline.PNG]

</p>

Notice that I initially designed the chassis with the baseboard mounted horizontally and the battery and motors underneath the baseboard. V3 is an example of this type of design, but this chassis was too wide to hit the two-way traffic specification. I tried making the width of the chassis the width of the baseboard, as seen with V4, but this chassis was too tall and thus too unstable. 
I then tried placing the battery behind the baseboard, as seen with V6, which is stable but is too long and fails the CAD test shown earlier. I eventually landed on V8 and V9, which have vertically mounted baseboards. The following table shows the specifications of the two final candidates:

| Field | Chassis V8 | Chassis V9 | Units |
| :--- | :--- | :--- | :--- |
| Weight | 422 | 397 | g | 
| Height | 108 | 108 | mm | 
| Width | 48 | 53 | mm |
| Length | 128 | 95 | mm |
| Max Length | 142 | 127 | mm |
| Center of Mass Height | ~47 | ~48 | mm |
| Max Speed Around Turn | ~0.44 | ~0.46 | m/s |

I used a scale and manufacturer weights for some components to find the weights of the two chassis. The height, width and length of the chassis were found from the CAD. The max length was calculated using the footprint chassis calculation shown earlier, by inputting the width specification into the first equation and seeing what length is needed to satisfy the equation.
The center of mass was calculated using the Onshape center of mass tool. 
The max speed around turn specification was calculated using the stability calculation shown earlier; the fast the robot can make the turn, the more stable the robot is. 

Notice how V8 and V9 have similar stability and center of mass height values, with the main differentiation being that V8 is less wide and longer than V9, and V9 is less long but wider than V8. When designing the chassis, I was not sure which specification is more advantageous for making the turn, so I decided to prototype both designs and do some testing. 

When I had the approximate weight, chassis designs and target speed of 1 m/s for the chassis, I was able to use this [tool](https://www.robotshop.com/community/blog/show/drive-motor-sizing-tool) to choose motor size. The calculations required a max torque of around 7 oz-in. I decided to go with Pololu mini plastic gearmotors, as Pololu is a popular robotics brand and the small motors would facilitate a small width for the chassis. 

The following image shows the prototypes for V8 and V9:
<p align="left">
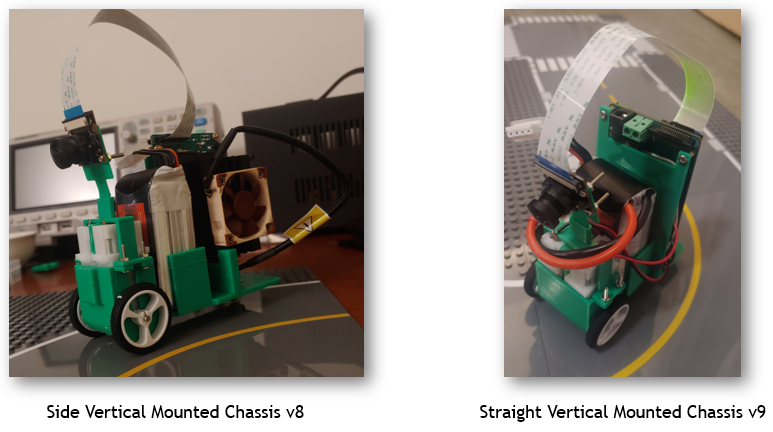
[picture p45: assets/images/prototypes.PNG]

</p>

In order to test the robots, I had to integrate GPIO into the software, as the original Jetbot uses an external motor driver that is controlled with I2C. I essentially ripped / commented out the I2C dependence in the critical software files and replaced it with GPIO control using the Jetson GPIO library. 
The Jetbot Mini software can be found [here](https://github.com/NVIDIA-AI-IOT/jetbot_mini/tree/main/jetbot).

I tested the robots using the [Basic Motion](https://github.com/NVIDIA-AI-IOT/jetbot/tree/master/notebooks/basic_motion) and [Road Following](https://github.com/NVIDIA-AI-IOT/jetbot/tree/master/notebooks/road_following) examples from the Jetbot repository. 

It turns out that V9 is the better chassis choice as for V8, when looking at the back view of the chassis, the center of mass is shifted slightly to the right due to the mounting nature of the baseboard. This means the left motor does get good traction with the ground, and so the V8 chassis has trouble turning to the rigth. I discovered this after noticing the robot having trouble turning right, and when I placed pressure on the left part of the chassis, the robot turned more easily. 
The following image visualizes the center of mass:

<p align="left">
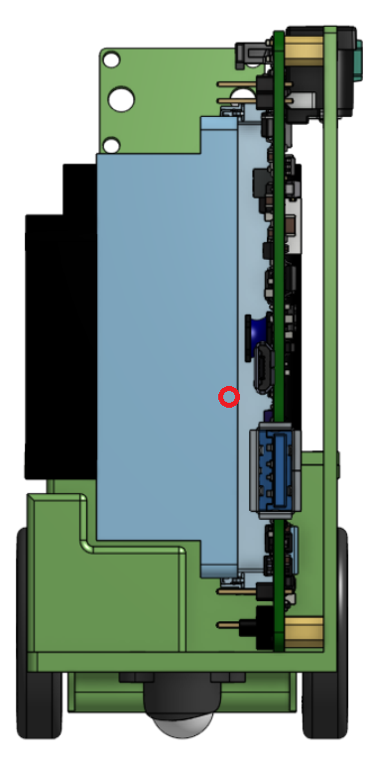
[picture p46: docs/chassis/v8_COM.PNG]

</p>

# Testing

The following video is the first autonomous test with Chassis V8 using the road following example:

https://user-images.githubusercontent.com/46247601/129984340-f981e0b2-2672-4e5d-aa17-2972e07930d5.mp4

This robot was trained with about 200 images. Notice how the chassis' movement is very erratic and zig-zaggy, and also the Jetbot Mini turns too early into the curve. The first issues is still being worked on, but the second issue is because there is a disconnect between what the camera sees and the position of the Jetbot Mini. The camera see the start of the turn when the Jetbot Mini chassis is still in the straight lane; therefore the Jetbot Mini will attempt to turn too early into the LEGO road curve, resulting in the robot driving into the pegs as seen.

The following demo is with the robot trained with around 500 images, and shows the Jetbot Mini successfully making both turns on the inner lane. 

https://user-images.githubusercontent.com/46247601/129984599-95fc7e9d-4848-483c-b340-6b4a7af6433a.mp4

Once the Jetbot Mini was able to make the inner turn, it was time to test with two Jetbot Minis:

https://user-images.githubusercontent.com/46247601/129984885-23387ae3-7aee-4cf6-af51-94b3f8954990.mp4

This demo shows two-way traffic, but again the movement of the robots is very erratic and jerky. Notice how when the Jetbot Mini moves, often one wheel is fixed while the other moves; this is an issue with PID control, as it is telling one of the motors to stay fixed. 
A basic way to try to solve this jerky movement was to try and force a minimum speed for the motors, with the following video being the result:

https://user-images.githubusercontent.com/46247601/129985136-e89e5bc2-a0ea-4379-8e0a-cbaae4b6af59.mp4

The movement is a bit smoother, but still does not solve the main issue of the PID control telling one of the motors to much slower than the other. Note also that this method does not help at lower speeds, as the PID control will tell the motors to move at a similar rate as the forced minimum speed, and so you get less control. You can change the turn gain of the motors, but as you increase this value, the movement becomes less accurate. At high speeds, the Jetbot Minis movement becomes too erratic and inaccurate. 

Some possible ways to make the movement smoother are as follows:
* Train the robot with more images
* Understand the model and neural network, and tweak the PID so one of the motors is not off during movement. 
* Add a second camera for a second reference point. 
* Add wheel speed encoders to give the robot more data to parse through; currently the only form of feedback is the camera. 
* Check to make sure latency is not an issue.

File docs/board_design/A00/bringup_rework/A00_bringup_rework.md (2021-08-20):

# Bringup and Rework

## Bringup

Bringup is the process of testing and debugging the power rails, IO and critical features of the board. The bringup checklist can be found [here](https://github.com/NVIDIA-AI-IOT/jetbot_mini/blob/main/docs/board_design/A00/bringup_rework/Jetbot_Mini_A00_baseboard_bringup_v1.xlsx). Here are some more indepth tutorials on how to test the different features of the board.

### General Notes

* grep -rn "text name"
  * Find which files have the string
* chmod +x \*.py
  * To enable execute permissions
* When in vim, can search for strings with "/"
* Running something with "| less" will printout the error
* Can use something like "While true ; do ___ ; done" to test a command on an infinite loop, and use cntrl+c in a linux terminal to terminate the command

### Power Rails

Test Power rails with a multimeter! Nice and simple :)

### GPIO Control

1. Open a terminal on Jetson Nano
2. cd /sys/class/gpio
3. echo # > gpio
> To calculate #, use the pinmux spreadsheet for the Jetson Nano, find the corresponding GPIO number that you want to control, multiply the letter corresponding to 0 - A, 1 - B, 2 - C, etc and add the constant. For example, GPIO13 corresponds to GPIO3_PE.06 on the pinmux spreadsheet, the letter E corresponds to 4, so # = 4 * 8 + 6  = 38
4. cd gpio#
5. echo out > direction
6. echo # > value, where # is 1 or 0 to set the GPIO value

### Testing Motors

Use the GPIO control tutorial, with the motor pins corresponding to the following:

From left to right: Jetson Nano GPIO Name, Pin number, GPIO number, GPIO with calculated #, Tegra Name

* Motor A / 1
  * A1: GPIO05, 128: H.07, gpio63, AP_WAKE_NFC
  * A2: GPIO04, 127: I.01, gpio65, NFC_INT
  * A2 (rework): GPIO10, 212: gpio169, LCD_BL_EN 
 > Note for A2, the GPIO is busy and you cannot access it, so a rework is necessary. I connected it to GPIO10
  * PWMA: GPIO07_PWM, 206: V.00, gpio168, LCD_BL_PWM (pin 32 on 40 pin header)
* Motor B / 2
  * B1: GPIO03, 126: I.02, gpio66, GPS_EN
  * B2: GPIO02, 124: H.06, gpio62, GPIO_PH6
  * PWMB: GPIO13_PWM, 228, E.06, gpio38, GPIO_PE6 (pin 33 on 40 pin header)

### Test USB 3.0

1. Connect USB device to module
2. Run: sudo mount | grep "/dev/sd" to mount the USB
3. Try to copy things over from the USB to the module using linux commands like cp or mv
4. Run: sudo umount /dev/sda1 to unmount the USB

> Sometimes you might overwrite part of the terminal line, to avoid this use the "resize" command

### Change I2C for OLED

1. Use i2cdetect -y -r 0 to ping the I2C0 lane for a module
2. Changed i2c_bus = 1 in “disp = Adafruit_SSD1306.SSD1306_128_32(rst=None, i2c_bus=1, gpio=1)”, to i2c_bus = 0 in stats.py in folder /home/jetbot/jetbot/jetbot/apps

### Check uUSB

1. Connect uUSB to host computer 
2. Enter recovery mode on baseboard by stopping boot over UART connection, and typing "enterrcm"
3. You should see a new device appear in device manager
 
### Test UART

> You should install PuTTY before stepping through this tutorial
> Note that the computer might not recognize the FTDI friend right away and might require additional drivers to be installed

1. Connect FTDI friend to baseboard and host computer (remember to connect rx to tx and vice versa on the baseboard!) with the baseboard OFF
2. Open up device manager and look for “USB Serial Port” under “Ports (COM &LPT)”
3. Open up PuTTy, go to serial tab, change Serial Line to COM port that the FTDI friend is detected under, and change speed to 115200 
4. Click Open, then power on the Jetson Nano module and you should see the Jetson Nano going through the boot up process

### Test Fan

1. Open up a terminal on the Jetson Nano module
2. cd /sys/devices/pwm-fan
3. From here you can run "cat cur_pwm" to read current PWM value, and "echo # > target_pwm" to change PWM to #
4. Enable tach with "echo 1 > tach_enable" and measure rpm with "cat rpm_measured"

### Camera

1. Open up a terminal on the Jetson Nano module
2. Run "gst-launch-1.0 nvarguscamerasrc ! nvoverlaysink", and you should see the camera start and wait for data
3. You can also try "gst-launch-1.0 nvarguscamerasrc sensor_id=0 ! 'video/x-raw(memory:NVMM),width=1920, height=1080, framerate=30/1, format=NV12' ! fakesink" to change the format of the camera output to test slower or faster speeds. 
4. You can also test camera with the "Road Following" Jupyter Notebook

### Wifi Dongle

1. Connect the Wifi Dongle to the USB3 port 
2. The Wifi Dongle shouldn't need any additional drivers and should connect to WiFi after you log in

## Bringup Findings

The following table summarized bring-up findings:

| Feature Test | Passed / WIP / Changed for A001 | Comments |
| :--- | :--- | :--- |
| USB 3.0 Type A | Passed | Able to transfer files, Wifi Dongle works |
| Camera Modules | Passed | Front camera works, test with B01 instead of A02!! |
| Fan | Passed | Able to get RPM readings and control speeds with PWM, used Noctua 40 mm |
| OLED | Passed | Need to change from I2C0 to I2C1 to match Jetbot |
| USB 2.0 Micro-B | Passed | Able to see device when in recovery mode |
| 10s Button Press Shutdown | Passed | Need to optimize component choice |
| Button Power On | Passed | Resistor that connects button to circuit was NS, also requires removal of buffer in power logic circuit |
| UART | Passed | Able to make serial connection using FTDI friend |
| 5V_AO Rail | Passed | Turns on to around 5.05V |
| 1V8 Rail | Passed | Boots up to around 1.801V |
| Battery Charger | WIP | Follows charging curve as expected, regulates battery voltage at 12.60 V, but CHGOK does not turn off |
| Low Battery LED | WIP | Working as expected, but voltage threshold (7.5V) is too low and getting flickering |
| 5V Rail | Changed for A01 | Turns on to around 5.20 – 5.38V |
| 3V3 Rail | Changed for A01 | Boots up to around 3.25V, but needs rework to enable signal|
| Motor Control | Changed for A01 | Able to control both motors, but needed to rework MC_A2 to GPIO10 |
| Software Shutdown Request | Changed for A01 | Removed buffer that allowed this in order to turn on 5V rail |

## Rework

The following reworks were done to get the A00 baseboard ready for testing with Jetbot Mini. For more in depth detail on changes in A01 that address bring-up findings, see [here](https://github.com/NVIDIA-AI-IOT/jetbot_mini/blob/main/docs/board_design/A01/A01_design_justification.md).

<p align="left">
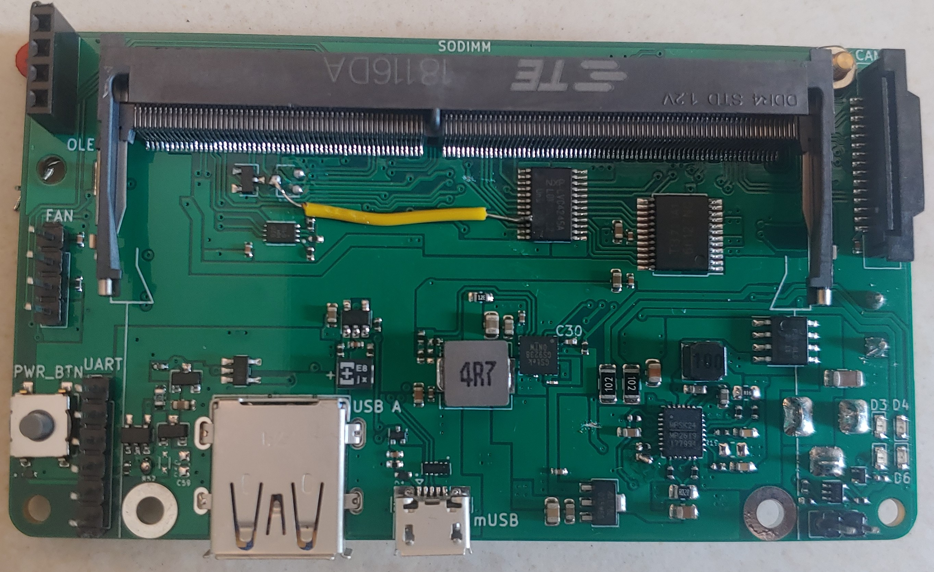
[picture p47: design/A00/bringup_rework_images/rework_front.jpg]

</p>

<p align="left">
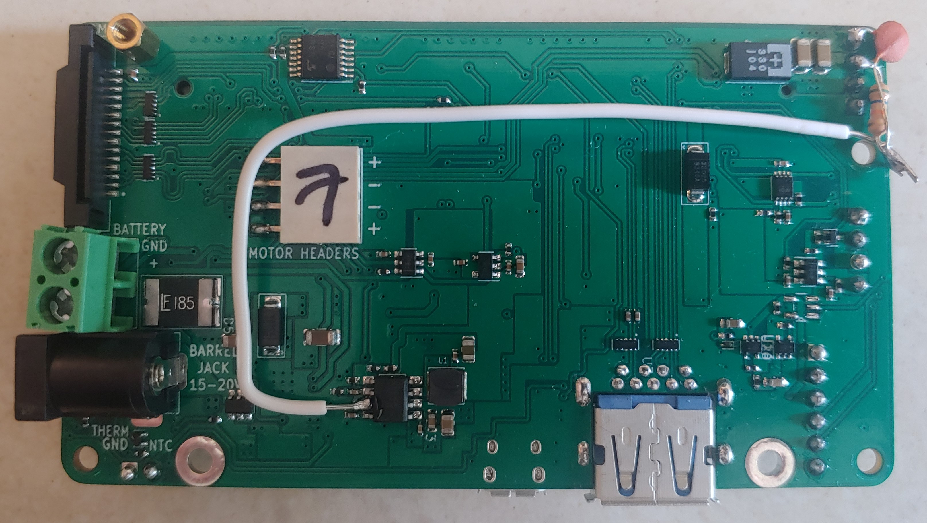
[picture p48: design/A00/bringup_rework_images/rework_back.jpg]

</p>

### No-Stuffed Components

<p align="left">
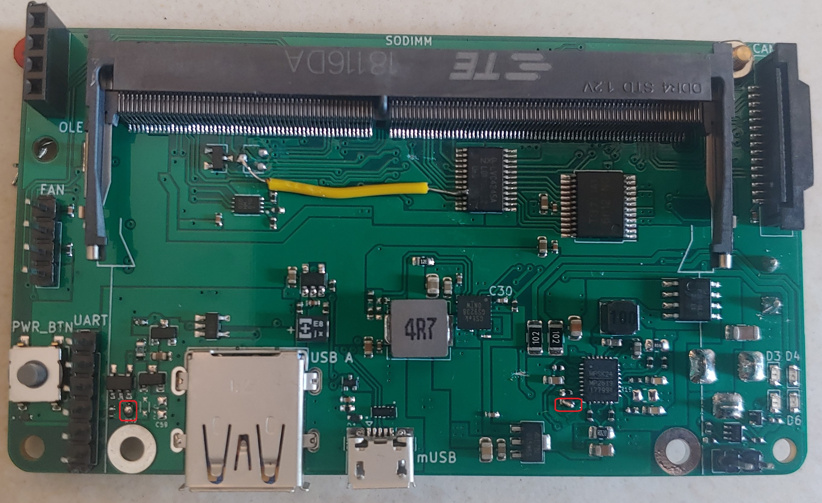
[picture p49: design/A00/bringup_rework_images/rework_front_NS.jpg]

</p>

<p align="left">
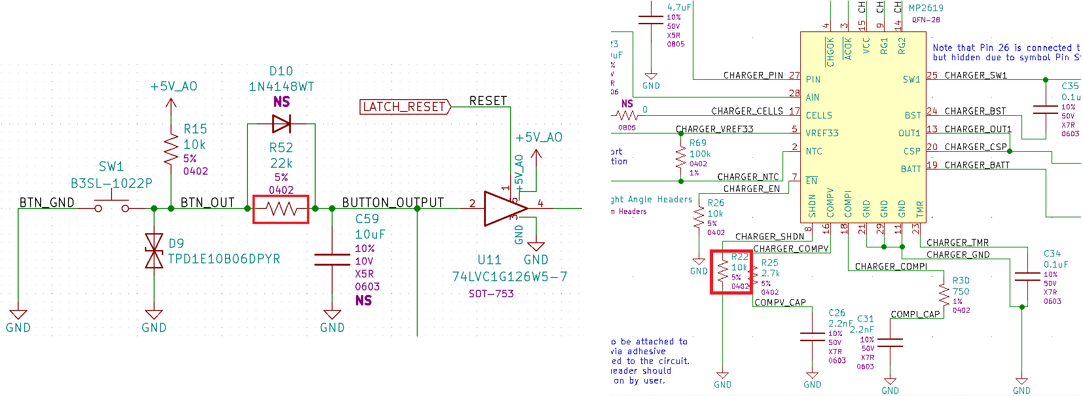
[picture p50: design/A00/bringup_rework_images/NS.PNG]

</p>

Some resistors that should have been assembled (stuffed) were not (no stuffed), and so I had to solder bridge the pads. 

### Motor Controller GPIO

<p align="left">

</p>

<p align="left">

</p>

GPIO04, which A2 was connected to, could not be controlled via software, so I cut the trace and rerouted that GPIO to GPIO10. 

### 3V3 Buck Converter Enable

<p align="left">

</p>

<p align="left">

</p>

<p align="left">

</p>

SYS_RST, which is used for the 3V3 Buck Converter enable signal, is on 1V8 logic, but the enable pin needs at least 2.2 V, so the 3V3 buck converter was not turning on. This was resolved by cutting the trace on the front and rerouting the enable to pin to 5V via an RC circuit set to charge to 98% of 5V after 20 ms to hit power sequencing requirements. 

### Power Logic Buffer

<p align="left">

</p>

<p align="left">

</p>

The SHUTDOWN_REQ signal was holding RESET low as the module is initially off, which means the power logic never turns on 5V, which never turns on the module. This loop prevents the baseboard from turning on. To get around this and test the board, the buffer connecting SHUTDOWN_REQ to RESET was removed, cutting off software shutdown capabilities but allowing the power logic to work as intended. 

### Motor Header Stabilization

<p align="left">

</p>

The motor headers were poorly soldered to the baseboard and so were flexing and at times pulling off the baseboard; I added additional solder to stabilize the headers.

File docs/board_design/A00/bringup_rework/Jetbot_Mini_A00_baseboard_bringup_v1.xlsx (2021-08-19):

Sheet: A00 Baseboard #1
Jetbot Mini A00 Baseboard Bring Up Check Items |  | Location/Ref Des | Measured | Expected | Pass or Fail | Comments |  | PASS
Visual and Mechanical Inspection |  |  |  |  |  |  |  | WIP
 | Visually check all SMT components for tombstoning | - |  | - | PASS |  |  | FAIL
 | Visually check for solder bridges | - |  | - | PASS | Note that R52 is deliberately solder bridged, as otherwise the button is not connected to the rest of the circuit
 | Check silkscreen | J13, J9, SW1, J14, J1, R52, D10, C59, J8, J7, J5, J6, J12, J2, J3 |  | - | WIP | Check R52, D10 and C59 as they were meant to be NS options and user should be able to find them easily. Other checks are connectors, I/O and other important notes. Make sure things look clean, no weird logos, make sure things are aligned and neat, no smudges. Note that D10 silkscreen is misaligned and clips into the pads of C59. C30 is marked with silkscreen for some reason? D7 silkscreen is covered by capacitor. R19 silkscreen is clipped by the resistor pads. Battery GND + is very confusing, rework (J12). D5 is marked for no reason. Barrel Jack Text is slightly clipped by U3 and C40. Need to add silkscreen for UART (J14), OLED (J13), Fan (J9).
 | Check U18, F1, J5 (DC Jack), C11, C46, D5, D8, L2, L3 | U18, F1, J5, C11, C46, D5, D8, L2, L3 |  |  | PASS | These footprints were made by me, so make sure that all the parts look soldered on correctly C11 and C46 look a little small for the components, can't see any of the pads underneath. Double check these component?
 | Module fitting in SODIMM connector | J1 |  | - | PASS
Short circuit Check
 | Check for short on Barrel_Jack_Vin | J5 |  | - | PASS
 | Check for short on Battery_PWR | J12 |  | - | PASS
 | Check for short on Charger_Output | C19 |  | - | PASS
 | Check for short on +5V_AO | U15 pin 1 |  | - | PASS
 | Check for short on +5V | L3 or J14 |  | - | PASS
 | Check for short on +3.3V | L1 |  | - | PASS
 | Check for short on +1.8V | U24 pin 5 |  | - | PASS
 | Check for short on microUSB VBUS, D+, D- nets | J7 |  | - | PASS | microUSB not working, so need to troubleshoot why
 | Check for short on Camera Nets |  |  | - | PASS
Voltage and Current Check
 | Charging Current | R38 | 1.4 A | 1.5 A | WIP | Use the current sense resistor R38, measure voltage across it and check V = iR for the current. Double check why the current value is off. | C denotes maximum charge rate, every battery has a specific maximum charge current, and worst case you can damage or destroy it.
 | Long Charge |  |  |  |  | Make sure when long charging, the voltage of the battery is properly regulated.
 | Charger_Output | C19 | 12.16 V | See Comments | PASS | If barrel jack plugged in, should be barrel jack voltage, and if battery plugged in, should be at battery voltage, if both plugged in then should be barrel jack voltage
 | 5V_AO | U15 pin 1 | 5.05 V | 4.75 - 5.25 V | PASS
 | 5V | L3 | 5.20 V | 5 V | WIP | After pressing button turns on. Initial state is off when power is plugged in? Voltage is a little higher than expected, perhaps because of incorrect values, also double check calculations. After plugging in Jetson Nano module, more like 5.10 V? | 12 V: 5.20 15 V: 5.20 19 V: 5.20
 | 3.3V | L1 | 3.248 V | 3.3 V | WIP | 3.3 V enable signal @3.387 V even though module is not plugged in???? Because the pin is floating, should go low once the module is plugged in, double check the pullups on all the datasheets.
 | 1.8V | U24 pin 5 | 1.801 V | 1.8 V | PASS
Functional Check
 | 10s button press shutdown | Short R52 and hold PWR_BTN |  |  | PASS | Once the module is powered on, should turn off the module.
 | Button Power On | Press PWR_BTN after shutting off the module with 10s press down |  |  | PASS | Initial state is off when power is plugged in????? However when you press button, 5V turns on as expected
 | Software Shutdown Req | After powering on the module, shutdown with software |  |  | FAIL | Cannot shutdown from software, had to remove buffer as it was pulling RESET low always, which never turns on the 5V buck converter, which never powers on the module.
 | UART | Power on with barrel jack, Connect FTDI friend to baseboard and host computer |  |  | PASS | Check if you can create a serial connection with Putty and login to the Jetson Nano. Was able to do this after making modification to 3V3 buck converter enable signal. Does 5V need to be connected? Note that PWR_LED will turn on even if just UART is connected Switch Rx and Tx on A01 to make compatible with FTDI dongle
 | Force Recovery from UART (check microUSB) | Power on with barrel jack or battery, connect FTDI friend to baseboard |  |  | PASS | Onced powered on, use Putty to create a serial connection, stop booting and type in "enterrcm", and check for device in Windows Device manager Works at both 12 V and 19V?
 | Check PWR_LED | D6 |  |  | PASS | Turns off and on as expected
 | Get Wifi Dongle Working |  |  |  | PASS | Download drivers, establish a wifi connection, try to log in via ssh.
 | Check ACOK | D3 |  |  | PASS
 | Check CHGOK | D4 |  |  | PASS
 | Check USB 2.0 Type A | J8 |  |  | PASS | Connect mouse or keyboard, or connect a USB drive and see if it appears. Make sure to confirm that your peripherals are either USB 2.0 or USB 3.0. Can also use lsusb to check the list of USB devices connected, lsusb -v will print out speed (do this from a terminal on the Nano).
 | Check USB 3.0 Type A | J8 |  |  | PASS | Connect mouse or keyboard, or connect a USB drive and see if it appears. Make sure to confirm that your peripherals are either USB 2.0 or USB 3.0. Can also use lsusb to check the list of USB devices connected, lsusb -v will print out speed (do this from a terminal on the Nano).
 | Check Camera Modules | J2, J3 |  |  | PASS | Plug in camera module with B01 module connected, follow a tutorial to setup and use the camera. Should be plug in play
 | Check Fan | J9 |  |  | PASS | Solder headers, check if PWM and Tach are working, instructions Fan spins up
 | Check OLED | J13 |  |  | PASS | Solder headers, connect display, control from L4T? Simply flash fresh SD with jetbot image, OLED display should light automatically once wifi is connected
 | Test Low Battery LED | D7 |  |  | PASS | Perhaps use power supply and test? Or try to drain battery somehow? Let it run with Jetbot and see if the LED turns on Test with power supply, without connecting the barrel jack
 | Check Motor Control | U6 |  |  | PASS | Plug in some motors, see if you can control the motors from L4T, see what happens with the motors. Look for tutorial online. Control some GPIO and motors.
 | Check NTC | J6 |  |  | PASS | If you short the pins, battery should stop charging. This mean battery temperature is too high so stop charging (NTC means decreasing resistance when increasing temperature)
 | Auto power ON |  |  |  | FAIL | When power is connected, there is no jumper like on the original Jetson Nano developer kit to disable auto power on? Should still auto power on, double check RC circuitry?
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

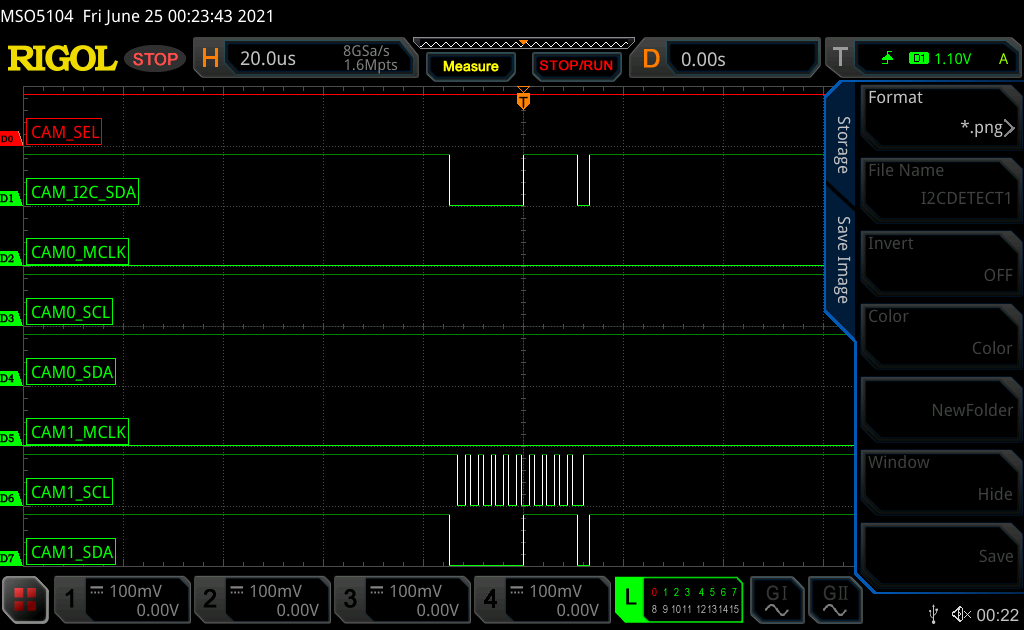
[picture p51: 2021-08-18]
docs/board_design/A00/bringup_rework/camera/I2CDETECT1.png

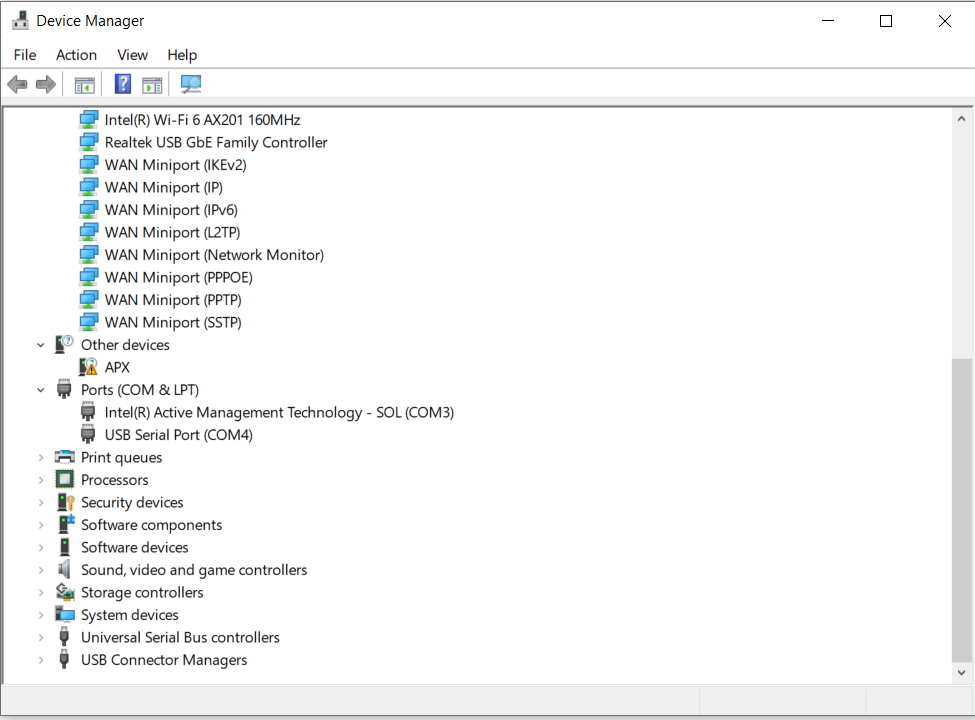
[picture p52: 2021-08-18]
docs/board_design/A00/bringup_rework/uUSB/device_manager.PNG

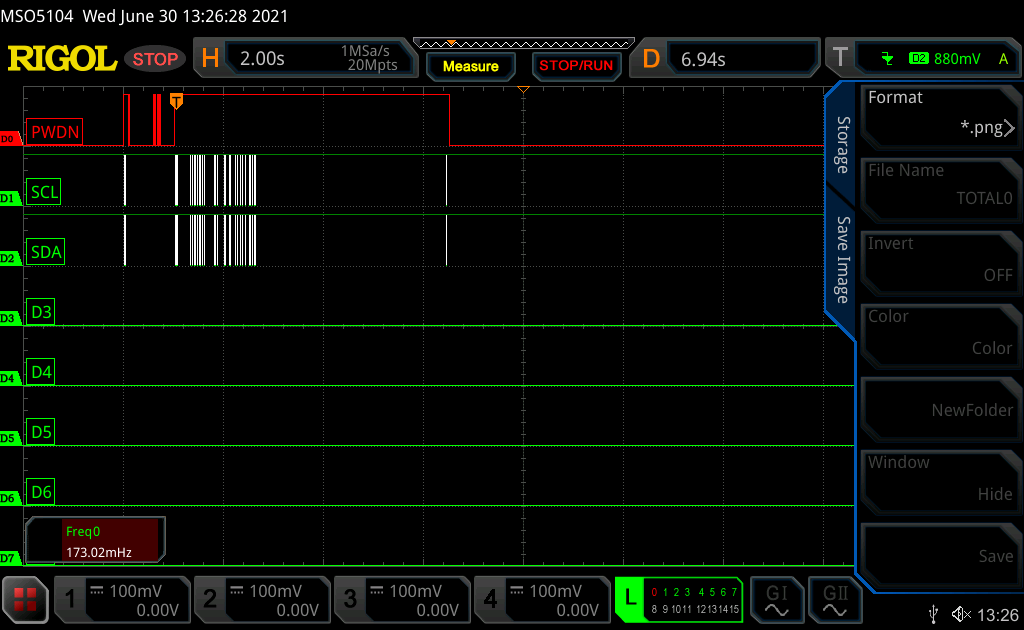
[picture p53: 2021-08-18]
docs/board_design/A00/bringup_rework/camera/TOTAL0.png

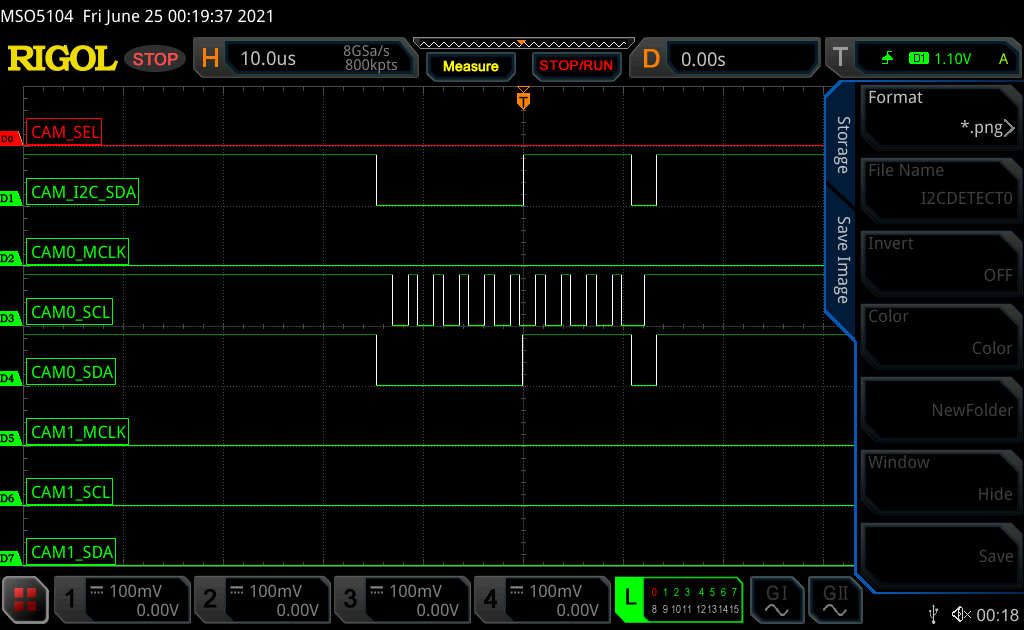
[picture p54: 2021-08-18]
docs/board_design/A00/bringup_rework/camera/I2CDETECT0.png

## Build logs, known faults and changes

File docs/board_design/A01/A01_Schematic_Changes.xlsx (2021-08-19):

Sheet: Rev 1
Change | Board # | ID / ME Impacts | Layout Impact | SW Impact | Status | Sheet / PDF Page No. | Note
1 | A00 | No | Yes | No | Implemented on A01 Schematic | Camera / 2 | Added R61, R66, R67, R68. Pullups on I2C lanes, needed to meet rise time requirements and for drive strength. Need large resistors as drive strength should not be too high, so chose 75k because this particular resistor value was used elsewhere on the schematic. B01 uses 47k
2 | A00 | No | Yes | No | Implemented on A01 Schematic | Motors / 3 | Removed U10, R59, C51, C56, as at the time thought SYS_RST needed to be level shifted from 1V8 to 3V3 as well, so combined into level shifter U10 on Nano_IO sheet. This will not work for SYS_RST however, need to implement open drain buffer.
3 | A00 | No | Yes | No | Implemented on A01 Schematic | USB / 4 | Removed R61, the bottom ferrite bead placeholder, as it does not help much and could cause some potential return path issues.
4 | A00 | No | Yes | No | Implemented on A01 Schematic | Nano_IO / 7 | Added R62 and R64 to give user the option between connecting 3V3 and 5V depending on the OLED display.
5 | A00 | No | Yes | No | Implemented on A01 Schematic | Nano_IO / 7 | Added U10, R59, C51, C56, as at the time thought SYS_RST needed to be level shifted from 1V8 to 3V3 as well, so combined into level shifter U10 on Nano_IO sheet. This will not work for SYS_RST however, need to implement open drain buffer.
6 | A00 | No | Yes | No | Implemented on A01 Schematic | Nano_IO / 7 | Switched UART_DEBUG_RX_3V3 and UART_DEBUG_TX_3V3 on FTDI connector to make compatible with FTDI friend.
7 | A00 | No | No | No | Implemented on A01 Schematic | Power_3 / 8 | Changed R41 from 56k to 35.7k and R42 from 10k to 6.8k to in accordance with proper calculations factoring in V_FB = 0.8 V
8 | A00 | No | No | No | Implemented on A01 Schematic | Power_3 / 8 | Changed R39 from 10k 5% to 10k 1% for more precise voltage output
9 | A00 | No | Yes | No | Implemented on A01 Schematic | Power_2 / 9 | Added R63 for hysteresis implementation for voltage comparator, noticed flickering on low power LED
10 | A00 | No | Yes | No | Implemented on A01 Schematic | Power_Logic / 10 | Tri-state buffer U29 added. R65 pullup added.
11 | A00 | No | Yes | No | Implemented on A01 Schematic | Nano_IO / 7 | Changed U23 from 74LVC4245A to 74LVC8T245

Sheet: Rev 2
Change | Board # | ID / ME Impacts | Layout Impact | SW Impact | Status | Sheet / PDF Page No. | Note
1 | A00 | No | Yes | No | Implemented on A01 Schematic | Motors / 3 | Added R59, U10, C51, and C56 back as previous design with level shifters would result in a loop, as the VCCA and VCCB rails rely on the SYS_RST rail to turn on
2 | A00 | No | Yes | No | Implemented on A01 Schematic | Power_1 / 7 | Added SW2, R69, and J6 to give user option of charging without thermistor
3 | A00 | No | Yes | No | Implemented on A01 Schematic | Nano_IO / 7 | Added Q9, Q10, R70 and R71 as a level shifter for SYS_RST

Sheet: Rev 3
Change | Board # | ID / ME Impacts | Layout Impact | SW Impact | Status | Sheet / PDF Page No. | Note
1 | A01 Rev 2 | No | Yes | No | Implemented on A01 Schematic | Power_2 / 9 | Changed U19 from LMV331SE-7 for cheaper part available on LCSC. Changed power from 5V to 5V_AO and 1V8 to 5V_AO so that the board doesn't need to be on to check battery status
2 | A01 Rev 2 | No | No | No | Implemented on A01 Schematic | Nano_IO / 7, Fan / 5, Power_1 / 6, Power_2 / 9 | R50 and R54 on Nano_IO, R8 on Fan, R21 and R69 on Power_1, R46 on Power_2 changed from 100k 5% to 100k 1%. Need better tolerance for Low Power LED Hysteresis and might as well change other 100k resistors to match and reduce part numbers for BOM.
3 | A01 Rev 2 | No | No | No | Implemented on A01 Schematic | Power_2 / 9 | Changed R48 from 100k 5% to 40.2k 1% for hysteresis.
4 | A01 Rev 2 | No | No | No | Implemented on A01 Schematic | Power_2 / 9 | Changed R63 from 470k 1% to 4.12M 1% for hysteresis.
5 | A01 Rev 2 | No | Yes | No | Implemented on A01 Schematic | Power_2 / 9 | Added U31, C60, C61 and R72 for level shifter between 5V and 1V8
6 | A01 Rev 2 | No | Yes | No | Implemented on A01 Schematic | Nano_IO / 7 | Changed MC_A2_1v8 from gpio04 to gpio0 due to software issue.
7 | A01 Rev 2 | No | Yes | No | Implemented on A01 Schematic | Nano_IO / 7 | Reverted change with U23, changed from 74LVC8T245 back to 74LVC4245A, as realized can simply flip the level shifter pins. 74LVC4245A is also the cheapest option
8 | A01 Rev 2 | No | Yes | No | Implemented on A01 Schematic | Camera / 2 | Changed R61, R66, R67, R68 to 47k to match B01, this value is also used for the hysteresis calculations

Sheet: Rev 4
Change | Board # | ID / ME Impacts | Layout Impact | SW Impact | Status | Sheet / PDF Page No. | Note
1 | A01 Rev 3 | No | Yes | No | Implemented on A01 Schematic | Camera / 2 | Added C63 and C64 to help Camera 3V3 lanes.
2 | A01 Rev 3 | No | No | No | Implemented on A01 Schematic | / 1 | Removed confluence link as this references NVIDIA internal document and the project is eventually going to be posted to github
3 | A01 Rev 3 | No | No | No | Implemented on A01 Schematic | Nano_IO / 7 | Added note to EEPROM section about 2.2k pull-up to 1.8V on module
4 | A01 Rev 3 | Yes | Yes | No | Implemented on A01 Schematic | Nano_IO / 7 | Added J10 to allow user to enter recovery mode more easily.
5 | A01 Rev 3 | No | No | No | Implemented on A01 Schematic | Several Pages | Changed 3.3V to 3V3 for various net names
6 | A01 Rev 3 | No | No | No | Implemented on A01 Schematic | Camera / 2 | Removed C63 and C64 as the intrinisic inductance of the ribbon cable used to connect to camera module will canel out any small spikes in current that 4.7uF capacitor is meant to smooth out.

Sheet: Rev 5
Change | Board # | ID / ME Impacts | Layout Impact | SW Impact | Status | Sheet / PDF Page No. | Note
1 | A01 Rev 4 | No | No | No | Implemented on A01 Schematic | All Sheets | Changed SODIMM with my own symbol
2 | A01 Rev 4 | No | No | No | Implemented on A01 Schematic | Nano_IO | Changed 74LVC4245A with my own symbol
3 | A01 Rev 4 | No | No | No | Implemented on A01 Schematic | Motor | Changed TB6612FNG with my own symbol
4 | A01 Rev 4 | No | No | No | Implemented on A01 Schematic | Camera | Changed TC7USB40FT with my own symbol
5 | A01 Rev 4 | No | Yes | No | Implemented on A01 Schematic | All Sheets | Changed SODIMM Footprint to TE's footprint
6 | A01 Rev 4 | No | No | No | Implemented on A01 Schematic | All Sheets | Moved all custom symbols to Jetbot_Mini_Symbols Library

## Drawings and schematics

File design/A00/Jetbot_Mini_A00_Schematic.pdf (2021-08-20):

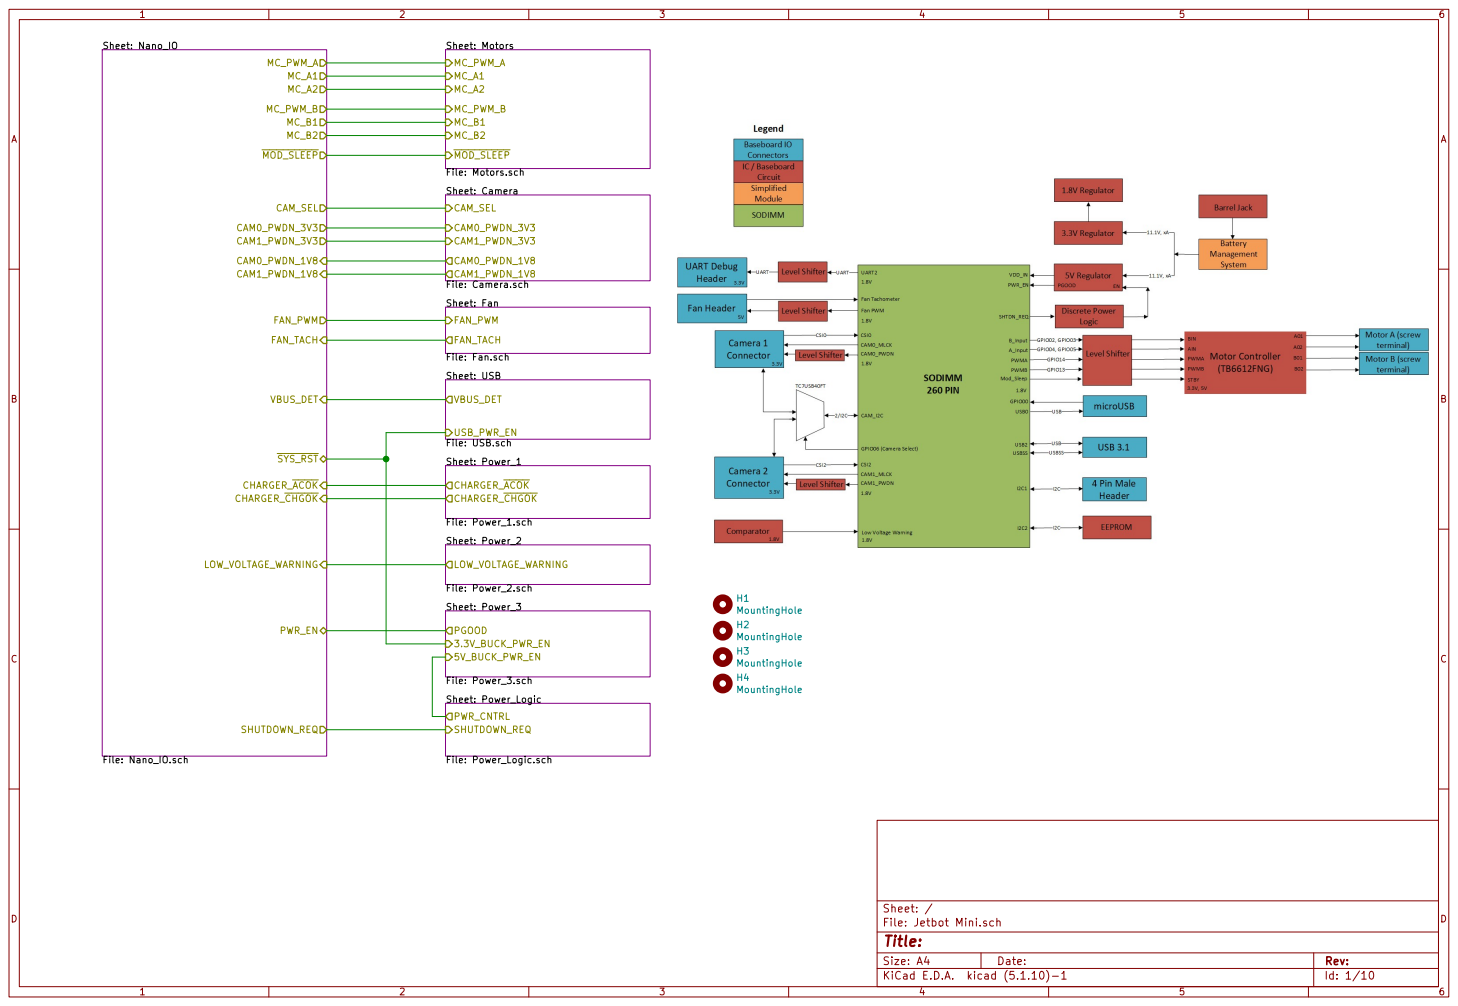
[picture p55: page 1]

CHARGER_ACOK CHARGER_CHGOK MOD_SLEEP
Sheet: Camera File: Camera.sch CAM_SEL CAM0_PWDN_1V8 CAM1_PWDN_1V8 CAM0_PWDN_3V3 CAM1_PWDN_3V3 Sheet: Fan File: Fan.sch FAN_PWM
CAM_SEL SHUTDOWN_REQ

Sheet: Motors File: Motors.sch MC_PWM_A MC_PWM_B MC_A1 MC_A2 MC_B1 MC_B2 MOD_SLEEP

Id: 1/10 Title: File: Jetbot Mini.sch Sheet: /

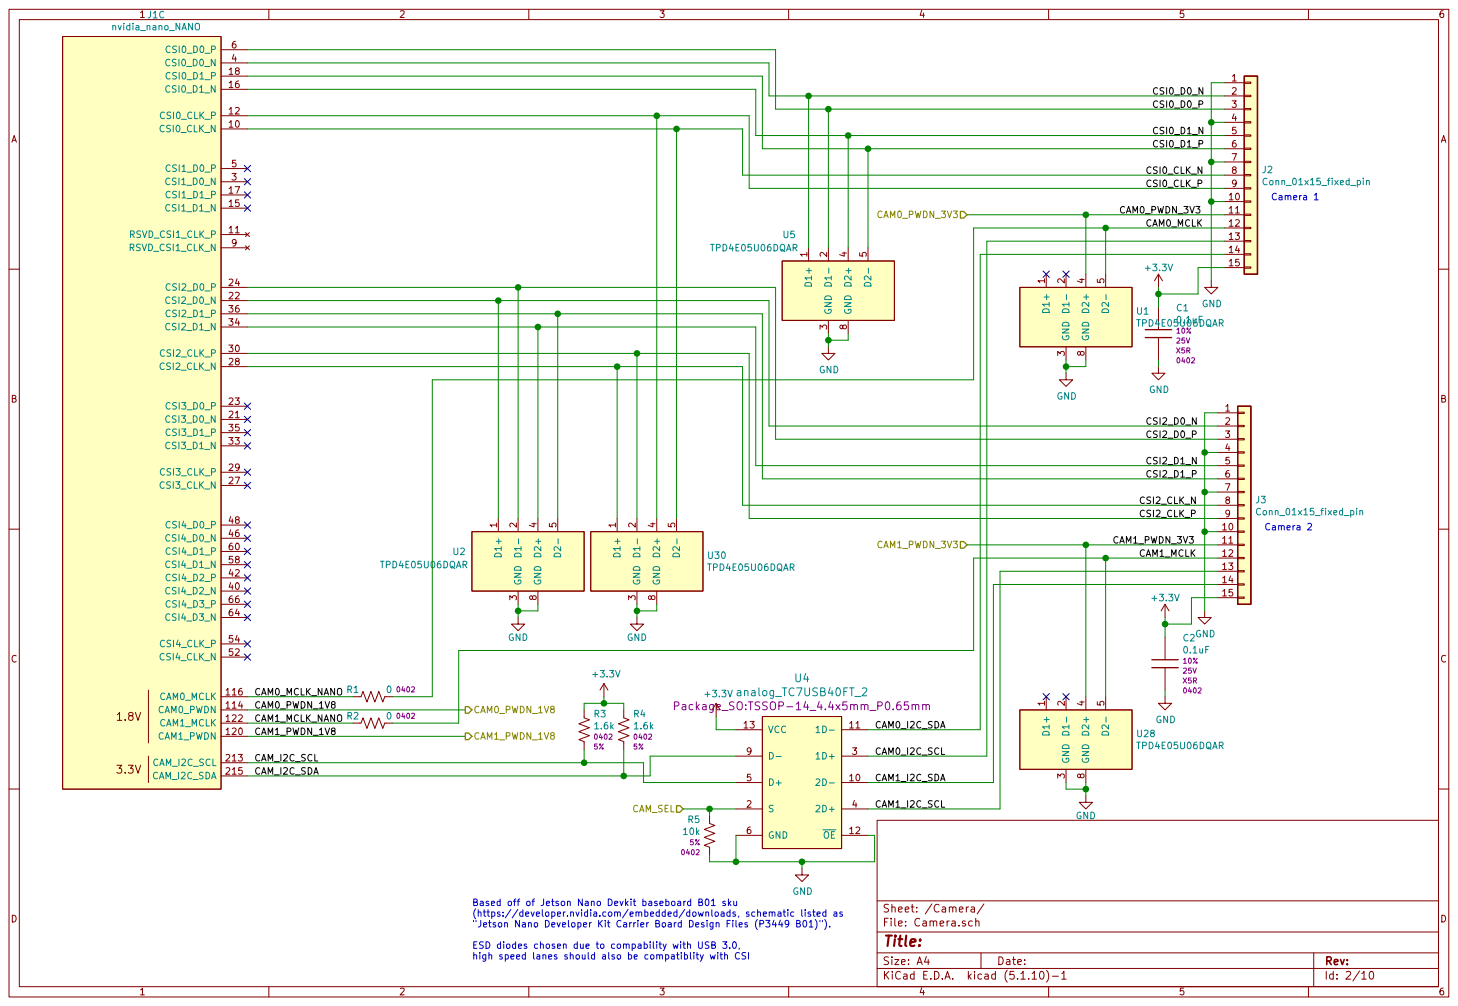
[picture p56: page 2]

CSI0_D1_P CSI0_CLK_N | 7

10

12
13
14
15

1 D1- 2 GND
Id: 2/10 Title: File: Camera.sch Sheet: /Camera/ D1+

"Jetson Nano Developer Kit Carrier Board Design Files (P3449 B01)").

ESD diodes chosen due to compability with USB 3.0,
high speed lanes should also be compatiblity with CSI

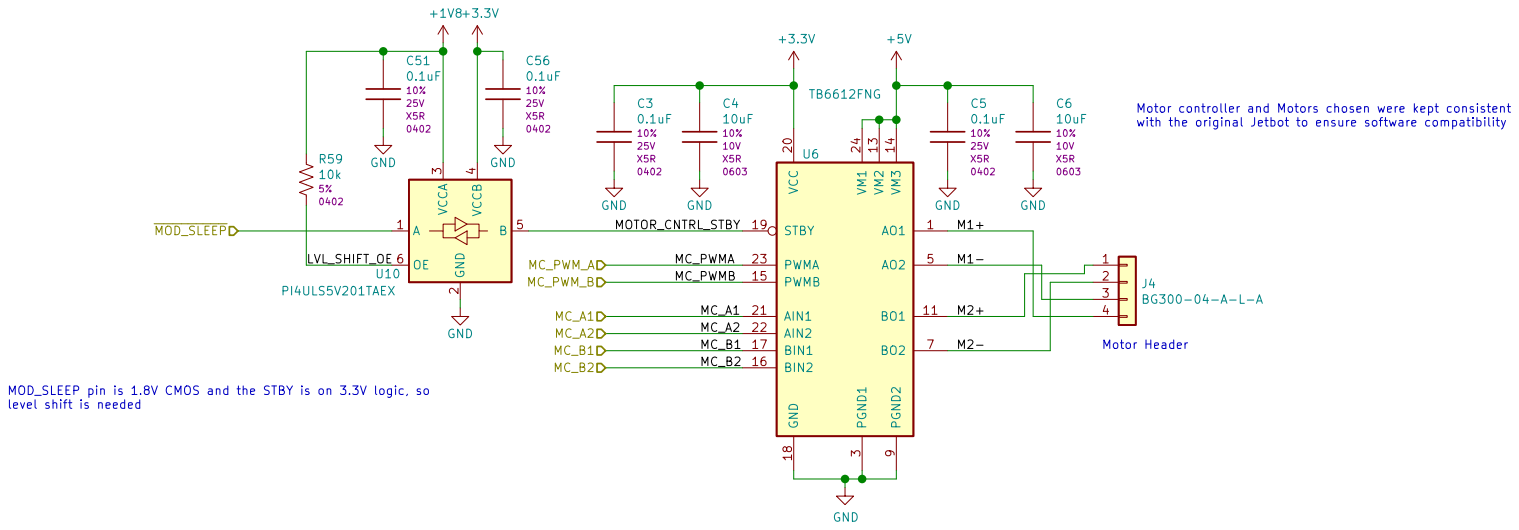
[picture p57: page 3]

with the original Jetbot to ensure software compatibility

Id: 3/10 Title: File: Motors.sch Sheet: /Motors/

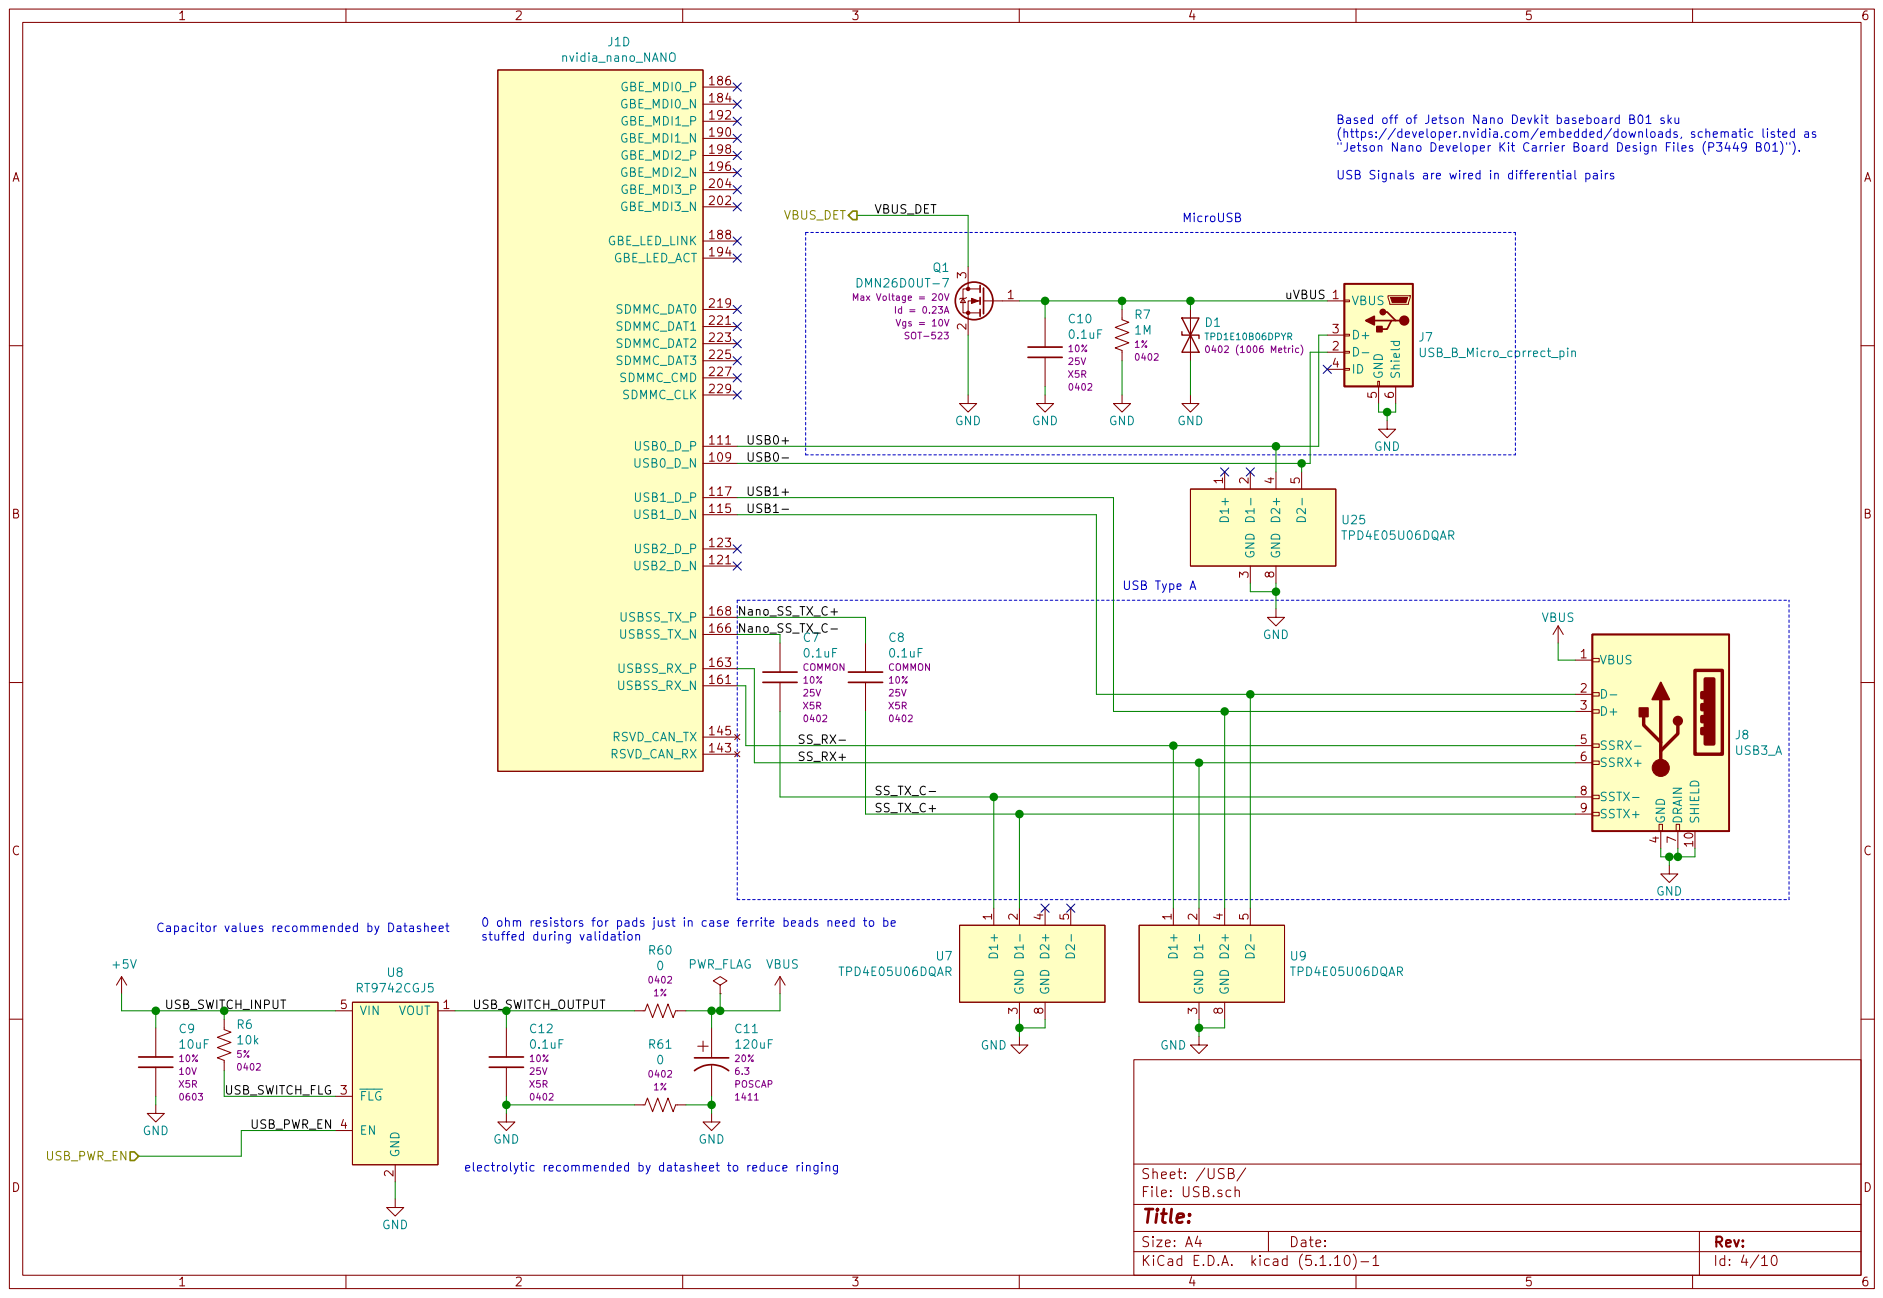
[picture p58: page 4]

Based off of Jetson Nano Devkit baseboard B01 sku (https://developer.nvidia.com/embedded/downloads, schematic listed as

"Jetson Nano Developer Kit Carrier Board Design Files (P3449 B01)").

USB Signals are wired in differential pairs

electrolytic recommended by datasheet to reduce ringing

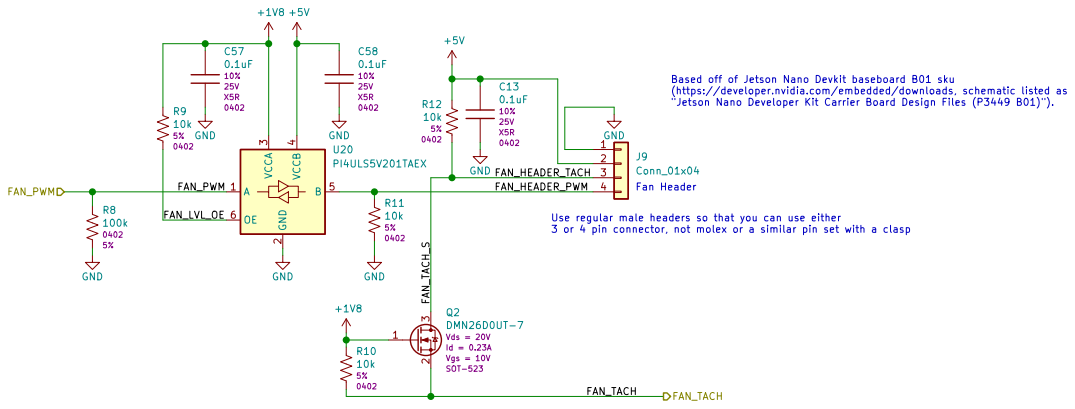
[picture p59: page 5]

3 or 4 pin connector, not molex or a similar pin set with a clasp Based off of Jetson Nano Devkit baseboard B01 sku (https://developer.nvidia.com/embedded/downloads, schematic listed as

"Jetson Nano Developer Kit Carrier Board Design Files (P3449 B01)").

Fan Header Use regular male headers so that you can use either

Id: 5/10 Title: File: Fan.sch Sheet: /Fan/

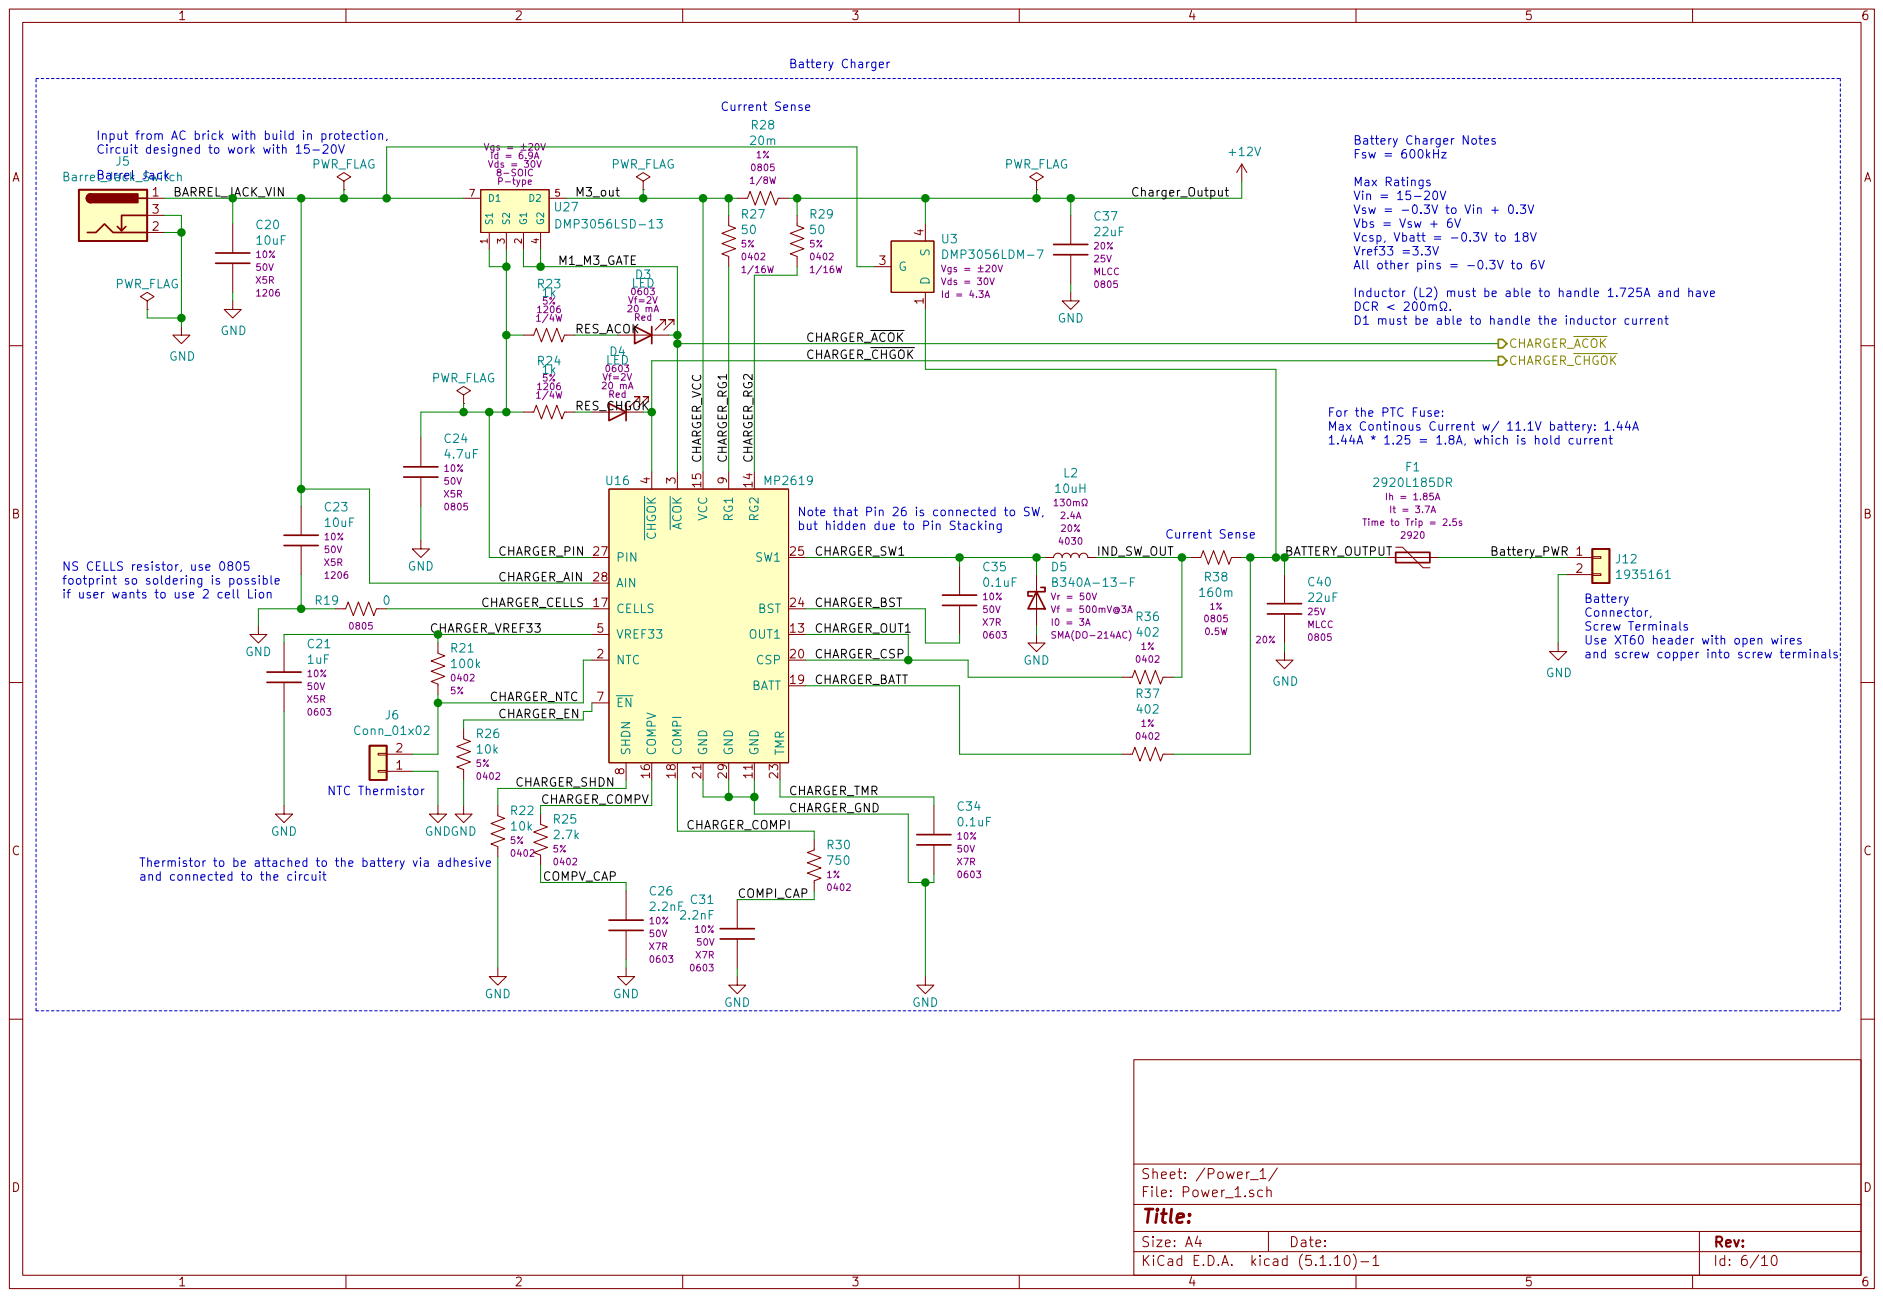
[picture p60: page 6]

Input from AC brick with build in protection,
Circuit designed to work with 15-20V

Battery Charger Notes Fsw = 600kHz Max Ratings Vin = 15-20V

Vsw = -0.3V to Vin + 0.3V
Vbs = Vsw + 6V
Vcsp, Vbatt = -0.3V to 18V
Vref33 =3.3V
All other pins = -0.3V to 6V

Inductor (L2) must be able to handle 1.725A and have DCR < 200m. D1 must be able to handle the inductor current NS CELLS resistor, use 0805

For the PTC Fuse: Max Continous Current w/ 11.1V battery: 1.44A

and screw copper into screw terminals Current Sense Thermistor to be attached to the battery via adhesive

footprint so soldering is possible

and connected to the circuit

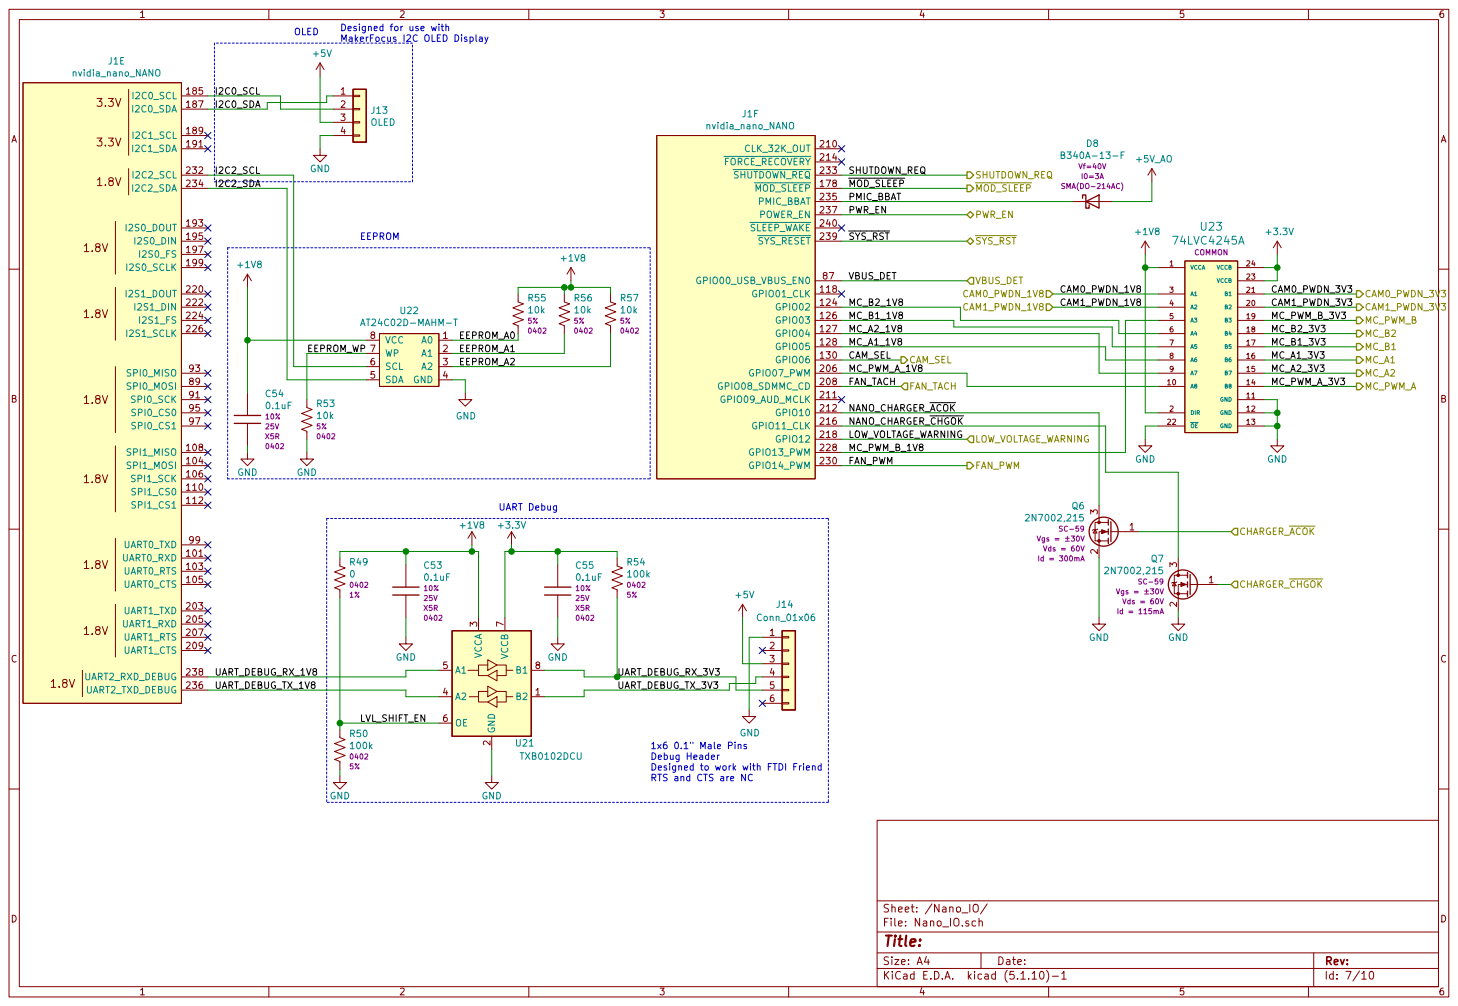
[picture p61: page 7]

Designed for use with
MakerFocus I2C OLED Display

I2C0_SDA
I2C2_SCL | 3

1x6 0.1" Male Pins Debug Header

Designed to work with FTDI Friend RTS and CTS are NC

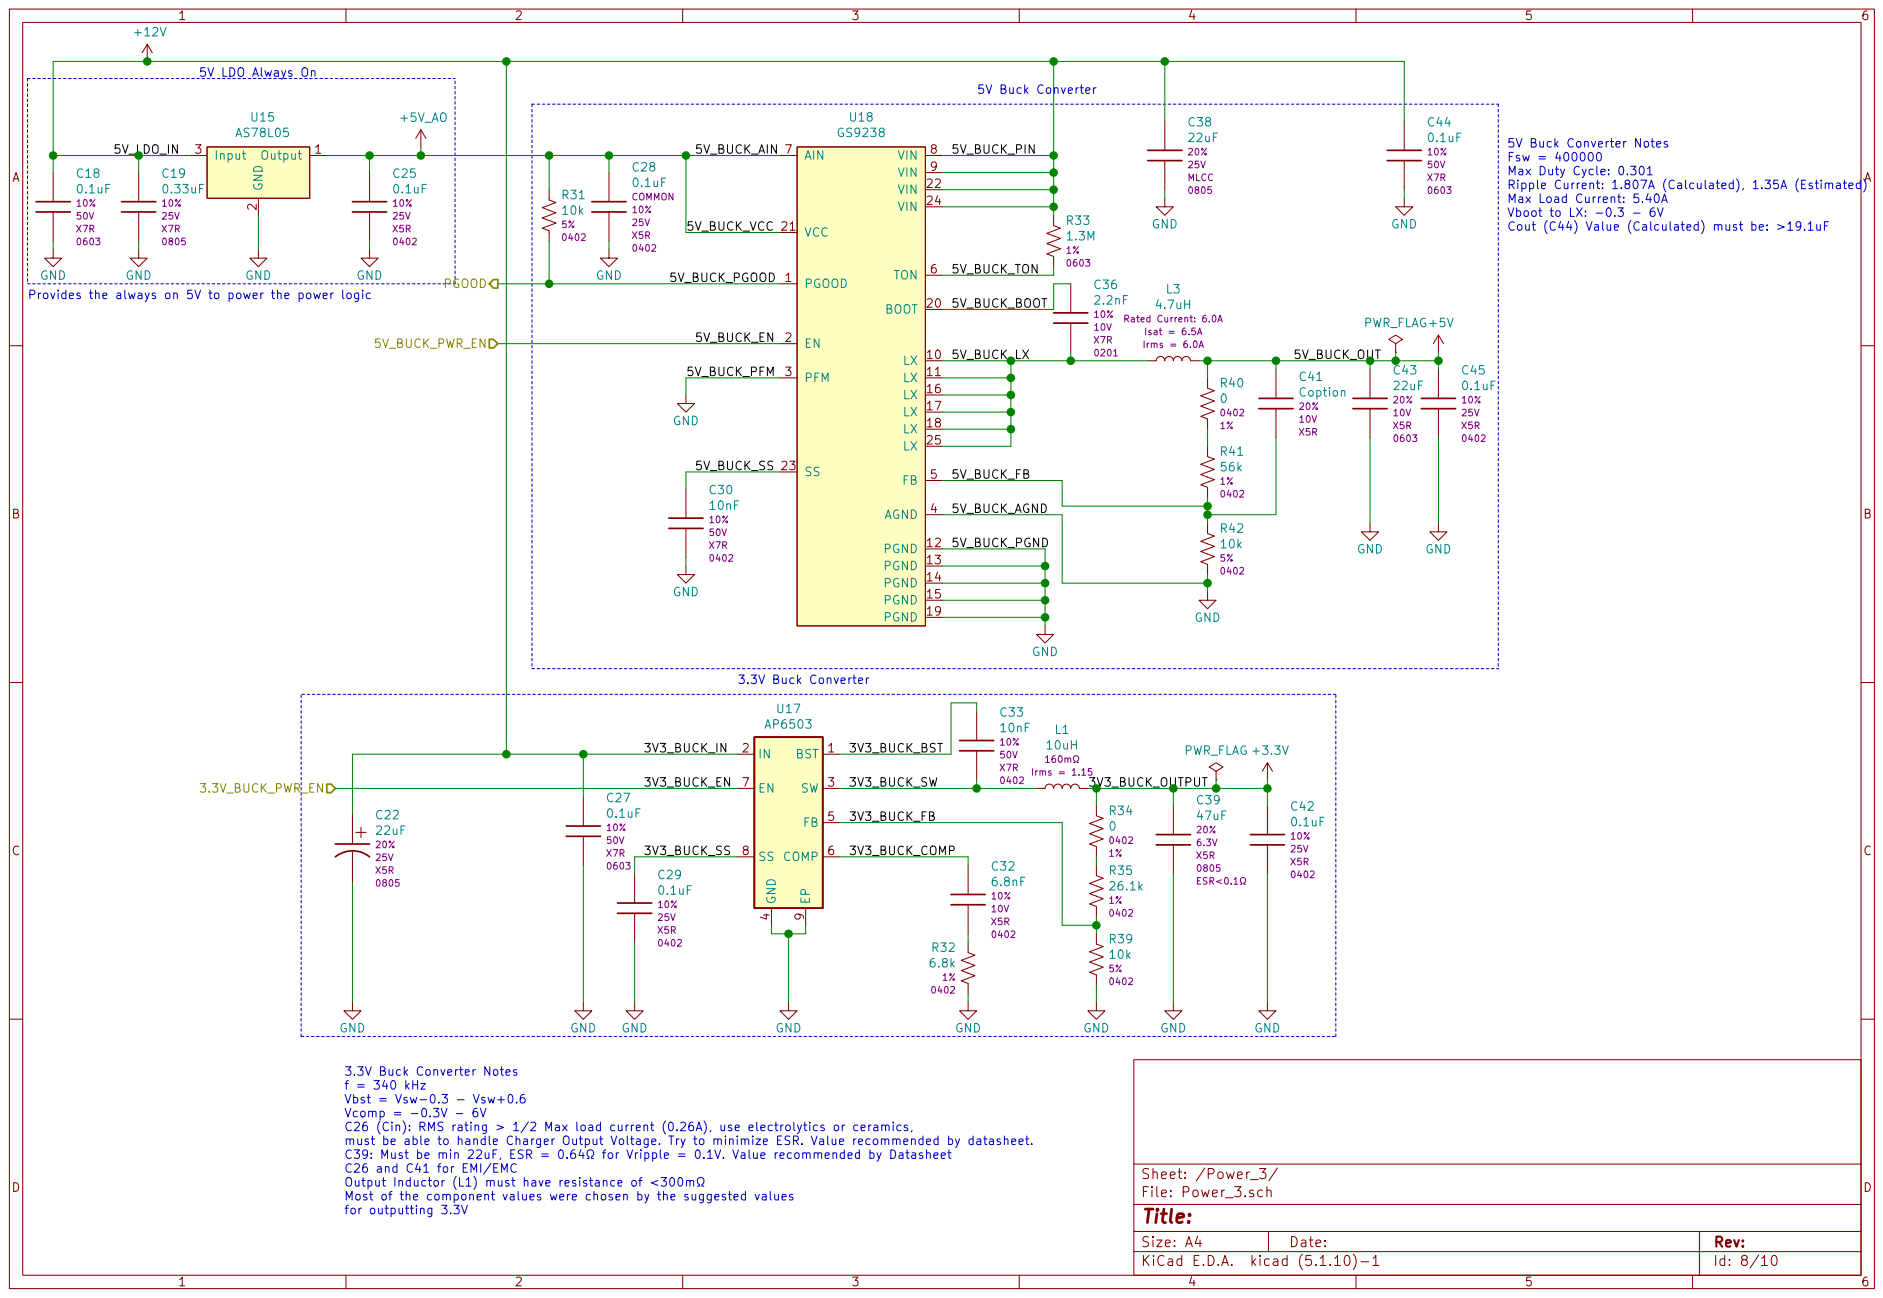
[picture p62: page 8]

5V Buck Converter Notes Fsw = 400000 Max Duty Cycle: 0.301

Ripple Current: 1.807A (Calculated), 1.35A (Estimated) Max Load Current: 5.40A

Vboot to LX: -0.3 - 6V Cout (C44) Value (Calculated) must be: >19.1uF

GND
Provides the always on 5V to power the power logic

4 FB 5 COMP 6 EN 7 SS 8 EP

3.3V Buck Converter Notes
f = 340 kHz Vbst = Vsw-0.3 - Vsw+0.6 Vcomp = -0.3V - 6V

C26 (Cin): RMS rating > 1/2 Max load current (0.26A), use electrolytics or ceramics,
must be able to handle Charger Output Voltage. Try to minimize ESR. Value recommended by datasheet.
C39: Must be min 22uF, ESR = 0.64 for Vripple = 0.1V. Value recommended by Datasheet C26 and C41 for EMI/EMC Output Inductor (L1) must have resistance of <300m

Most of the component values were chosen by the suggested values
for outputting 3.3V

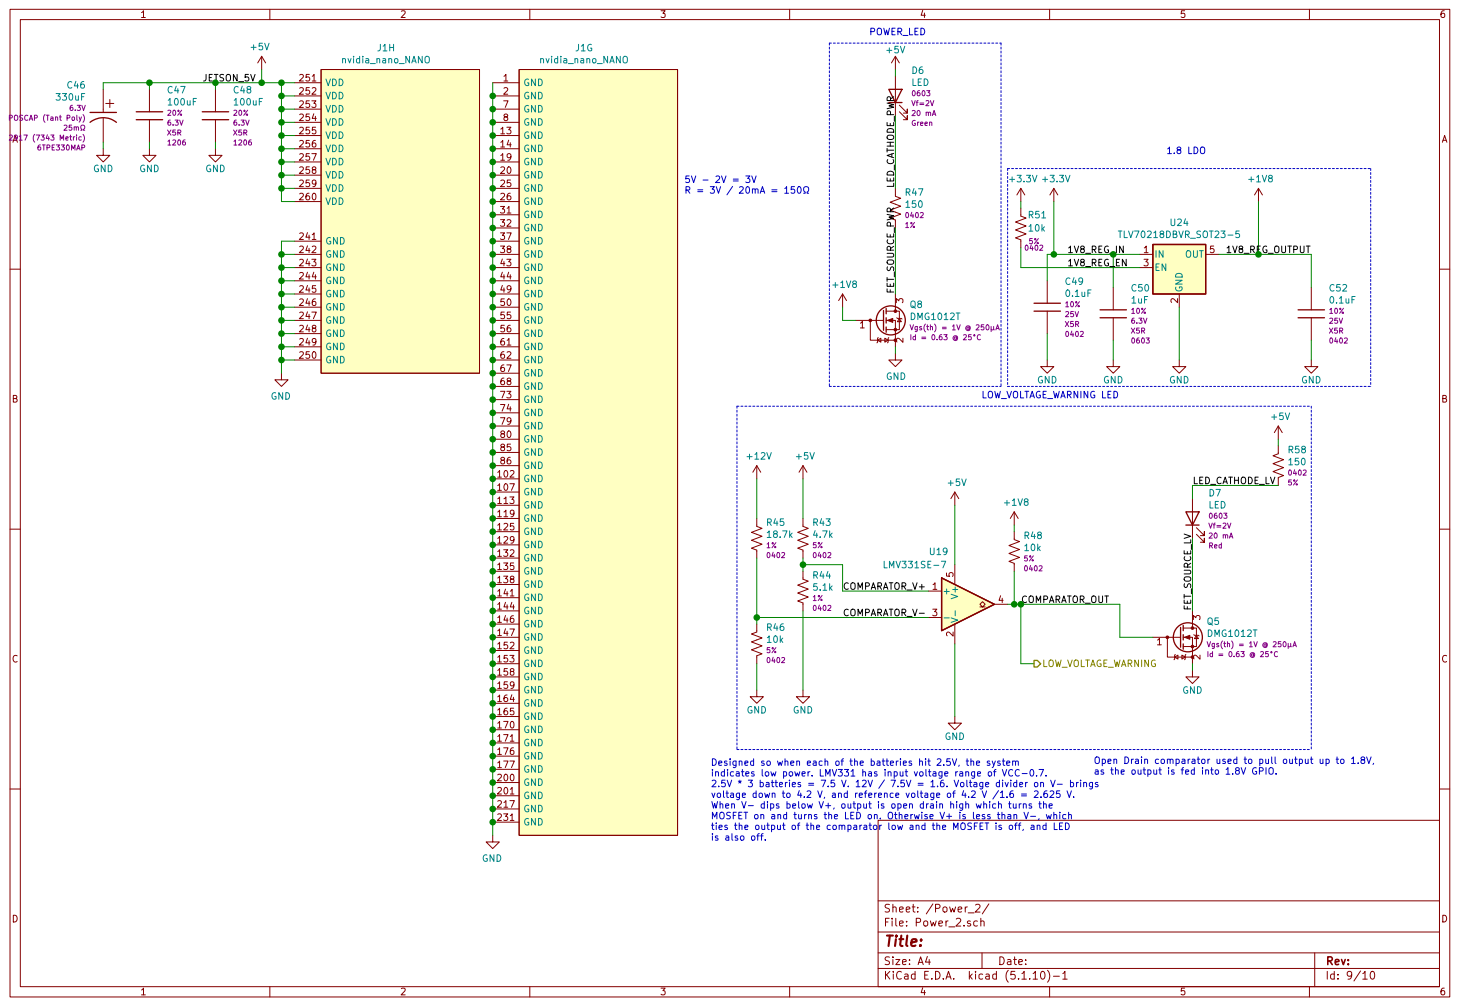
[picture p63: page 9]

Designed so when each of the batteries hit 2.5V, the system
indicates low power. LMV331 has input voltage range of VCC-0.7.
2.5V * 3 batteries = 7.5 V. 12V / 7.5V = 1.6. Voltage divider on V- brings
voltage down to 4.2 V, and reference voltage of 4.2 V /1.6 = 2.625 V.
When V- dips below V+, output is open drain high which turns the MOSFET on and turns the LED on. Otherwise V+ is less than V-, which

as the output is fed into 1.8V GPIO.

ties the output of the comparator low and the MOSFET is off, and LED
is also off.

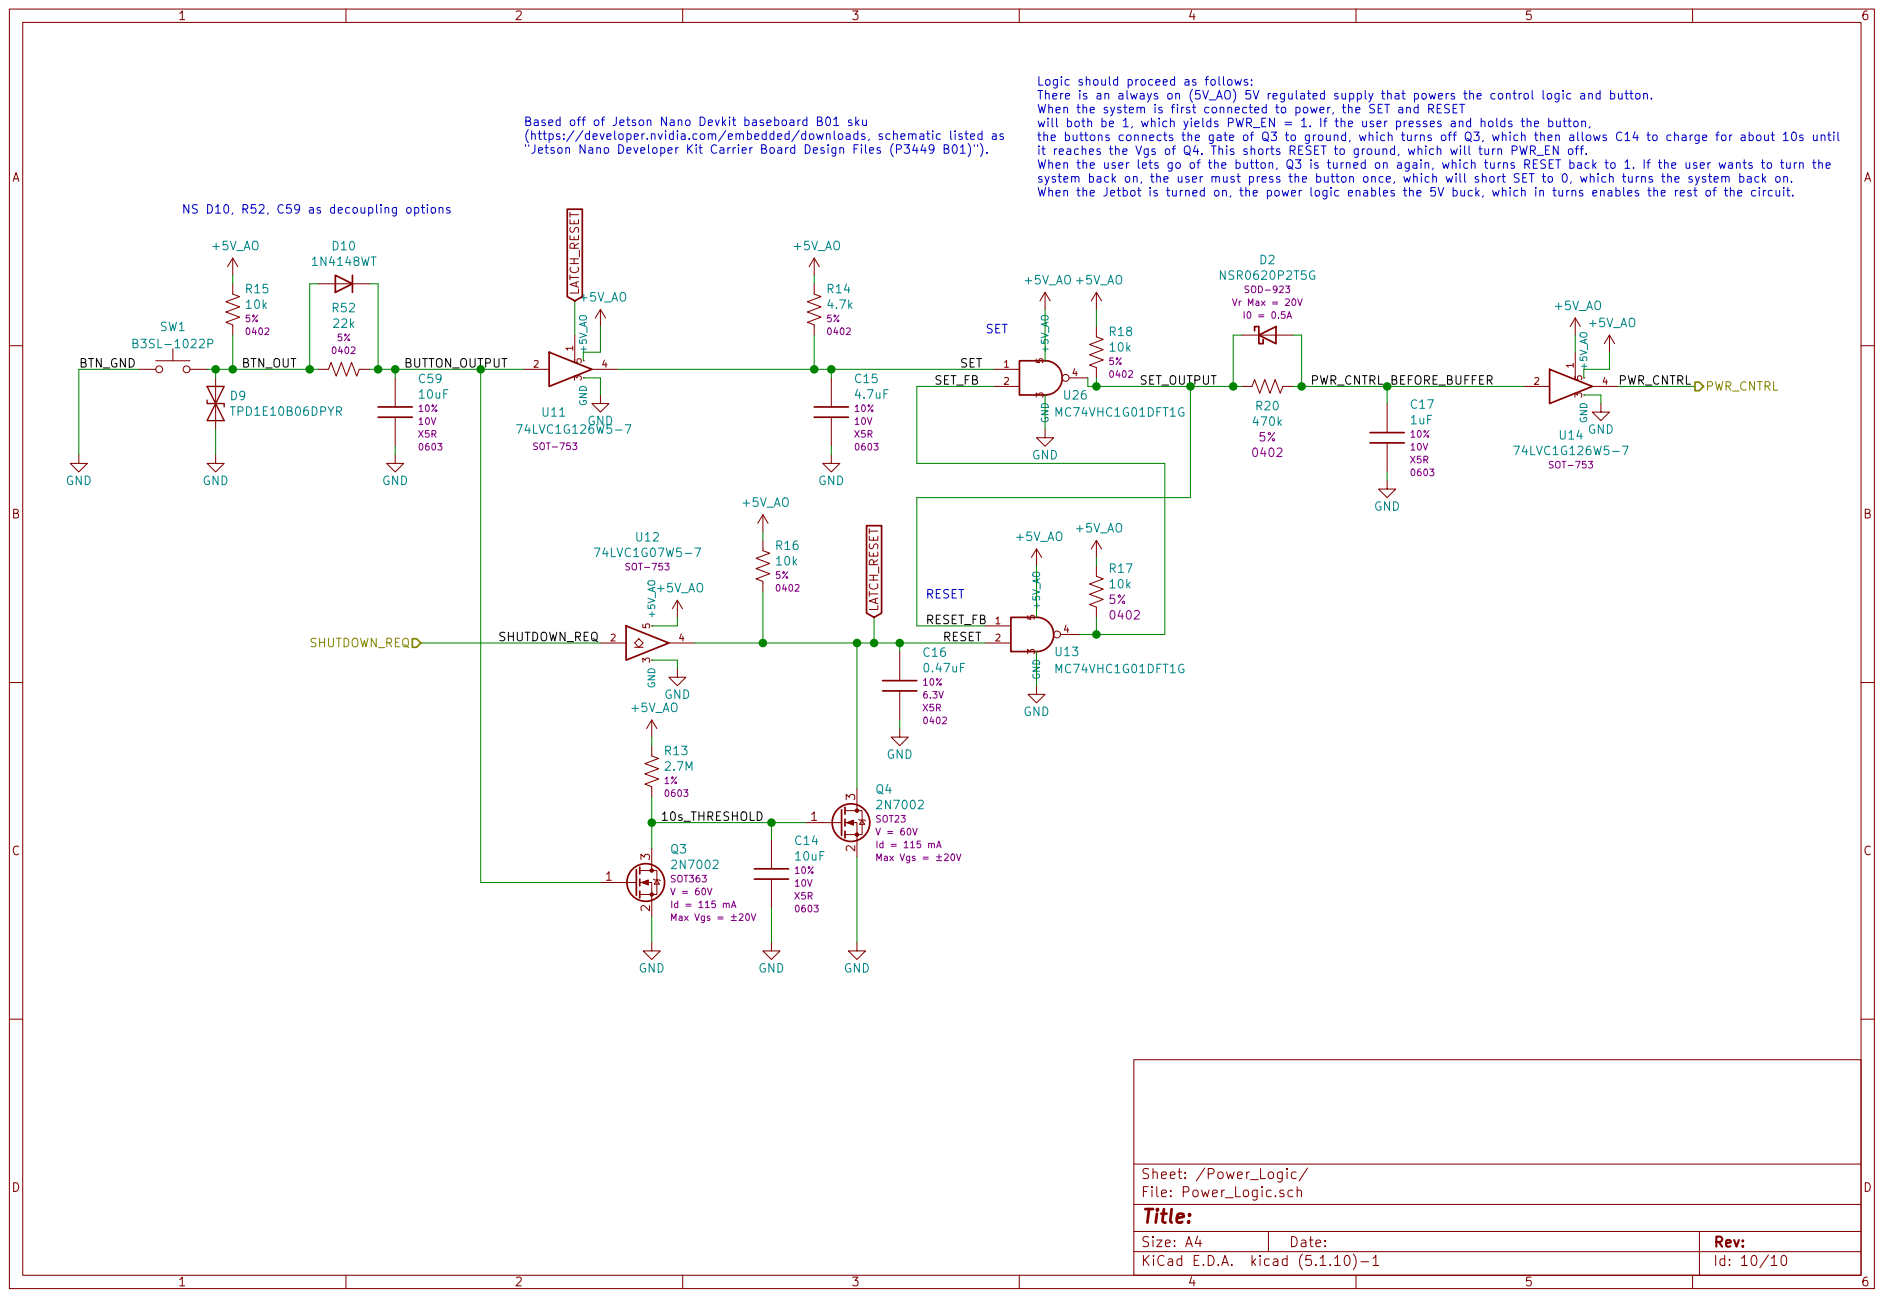
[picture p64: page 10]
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

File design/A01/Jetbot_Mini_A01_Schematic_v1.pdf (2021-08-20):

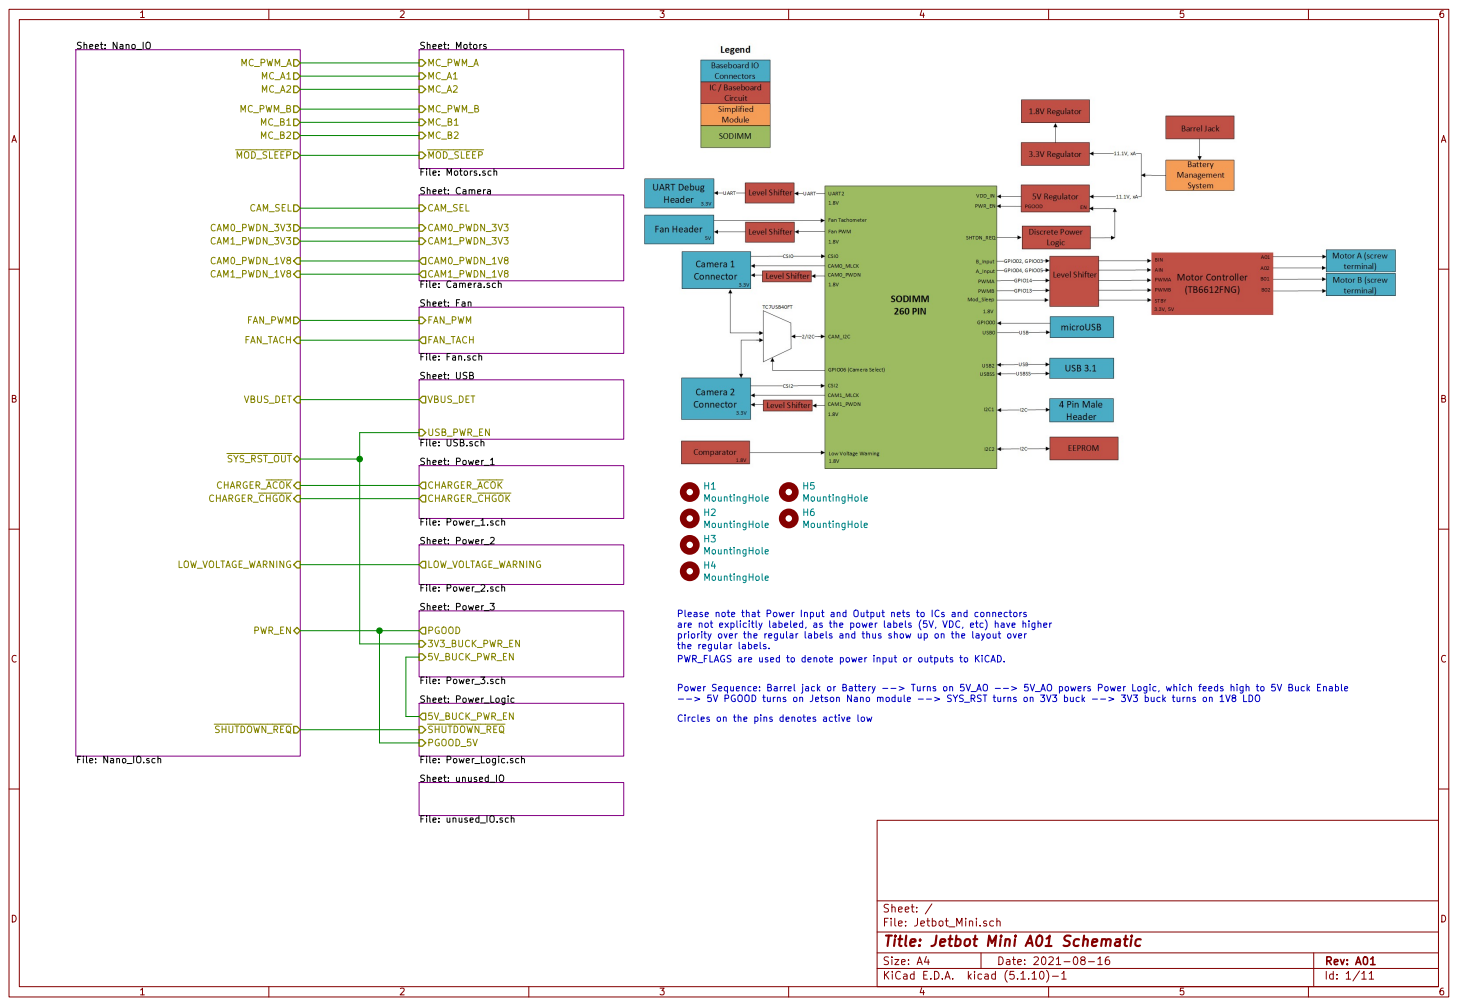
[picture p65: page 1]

CHARGER_ACOK CHARGER_CHGOK MOD_SLEEP
Sheet: Camera File: Camera.sch CAM_SEL CAM0_PWDN_1V8 CAM1_PWDN_1V8 CAM0_PWDN_3V3 CAM1_PWDN_3V3 Sheet: USB
CAM_SEL SHUTDOWN_REQ

Sheet: Motors File: Motors.sch MC_PWM_A MC_PWM_B MC_A1 MC_A2 MC_B1 MC_B2 MOD_SLEEP

Sheet: Fan File: Fan.sch FAN_PWM

Please note that Power Input and Output nets to ICs and connectors
are not explicitly labeled, as the power labels (5V, VDC, etc) have higher
priority over the regular labels and thus show up on the layout over
the regular labels.
PWR_FLAGS are used to denote power input or outputs to KiCAD.

Power Sequence: Barrel jack or Battery --> Turns on 5V_AO --> 5V_AO powers Power Logic, which feeds high to 5V Buck Enable
--> 5V PGOOD turns on Jetson Nano module --> SYS_RST turns on 3V3 buck --> 3V3 buck turns on 1V8 LDO
Circles on the pins denotes active low

File: Jetbot_Mini.sch Sheet: /
Id: 1/11 Title: Jetbot Mini A01 Schematic

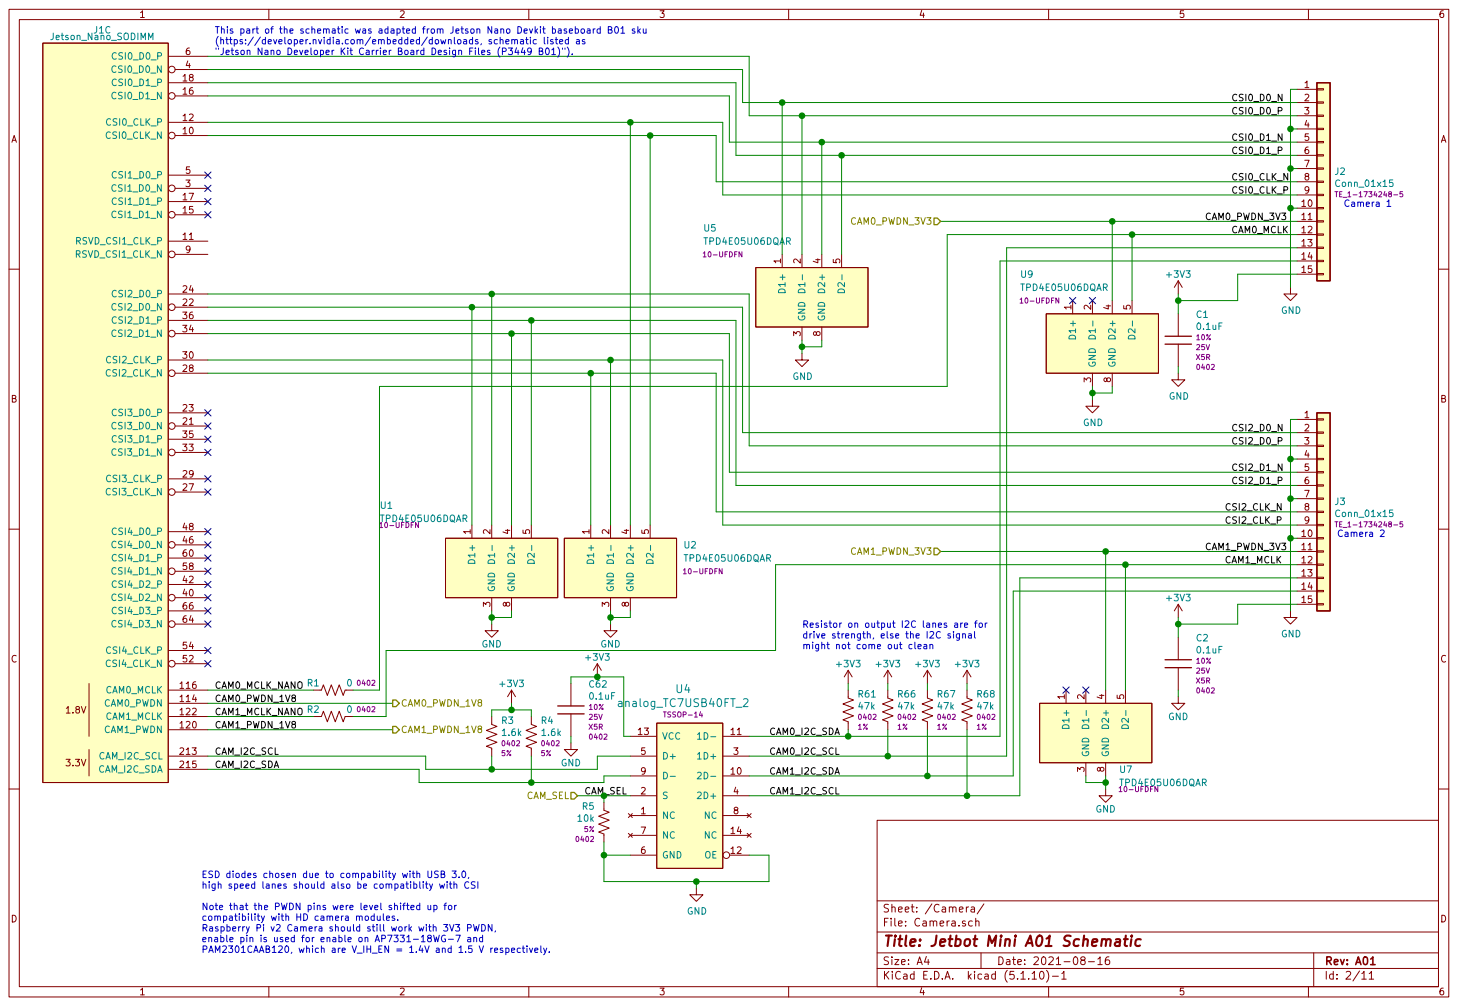
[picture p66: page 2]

(https://developer.nvidia.com/embedded/downloads, schematic listed as
"Jetson Nano Developer Kit Carrier Board Design Files (P3449 B01)").

CSI0_D1_N | 4 5

CSI0_CLK_N | 7 8

10 11 12

13
14
15

CSI2_D0_P | 3

7 8

drive strength, else the I2C signal

ESD diodes chosen due to compability with USB 3.0,
high speed lanes should also be compatiblity with CSI

Note that the PWDN pins were level shifted up for
compatibility with HD camera modules.
Raspberry Pi v2 Camera should still work with 3V3 PWDN,
enable pin is used for enable on AP7331-18WG-7 and

Id: 2/11 Title: Jetbot Mini A01 Schematic


This portion of the schematic was adapted from

with the original Jetbot to ensure software compatibility

MOD_SLEEP pin is 1.8V logic
and the STBY is on 3V3 logic, so level shift is needed

File: Motors.sch Sheet: /Motors/
Id: 3/11 Title: Jetbot Mini A01 Schematic


This part of the schematic was adapted from Jetson Nano Devkit baseboard B01 sku
10103594-0001LF Micro-B GND

R60 0 ohm resistor for pads just in case ferrite beads need to be
stuffed during validation
+5V GND

TPD4E05U06DQAR ESD diode pins can be the - or + data lines,
datasheet says each pin is a "ESD protected channel".

Electrolytic recommended by datasheet to reduce ringing

Capacitor values recommended by Datasheet
USB switch needed to protect the host, as the USB might be drawing
too much current, and you can power cycle the USB.

Id: 4/11 Title: Jetbot Mini A01 Schematic


"Jetson Nano Developer Kit Carrier Board Design Files (P3449 B01)").

File: Fan.sch Sheet: /Fan/
Id: 5/11 Title: Jetbot Mini A01 Schematic


Input from AC brick with build in protection,
Circuit designed to work with 15-20V

Charger Output Current Sense Current SenseNote that Pin 26 is connected to SW, but hidden due to symbol Pin Stacking

Battery Charger Notes Fsw = 600kHz Max Ratings Vin = 15-20V

VDC
SMA(DO-214AC) GND GND

Vsw = -0.3V to Vin + 0.3V
Vbs = Vsw + 6V
Vcsp, Vbatt = -0.3V to 18V
Vref33 =3V3 All other pins = -0.3V to 6V

Inductor (L2) must be able to handle 1.725A and have DCR < 200m. D1 must be able to handle the inductor current For the PTC Fuse: Max Continous Current w/ 11.1V battery: 1.44A

1.44A * 1.25 = 1.8A, which is hold current

with jumpers NS CELLS resistor, use 0805
footprint so soldering is possible
if user wants to use 2 cell battery. NS CELLS resistor means 3 cell battery operation.

Battery Connector, Screw Terminals Use XT60 header with open wires

inductors and output voltages can be found in the github repository. Have user short

1x3 Right Angle Headers SPDT

Thermistor to be attached to
the battery via adhesive
and connected to the circuit. Thermistor header should

be soldered on by user.

Sheet: /Power_1/
File: Power_1.sch
Id: 6/11 Title: Jetbot Mini A01 Schematic


MOD_SLEEP pin controls standby on motor controller, with VCC = 3.3V, V_IH (min) for standay pin is 2.31V,

This part of the schematic was adapted from Jetson Nano Devkit baseboard B01 sku

Designed for use with
MakerFocus I2C OLED Display,
which has an onboard LDO that accepts Vin = 1 - 6 V
and Vout = 3.3 V. Use 5V as 3V3 would yield a small
voltage drop in the output.

"Jetson Nano Developer Kit Carrier Board Design Files (P3449 B01)").

level shifter as 3V3 rail will not be on without SYS_RST

therefore needs level shifter. SYS_RST controls 3V3 buck enable

Use I2C1_SCL and I2C1_SDA for compatibility with Jetbot
SD Card Image
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

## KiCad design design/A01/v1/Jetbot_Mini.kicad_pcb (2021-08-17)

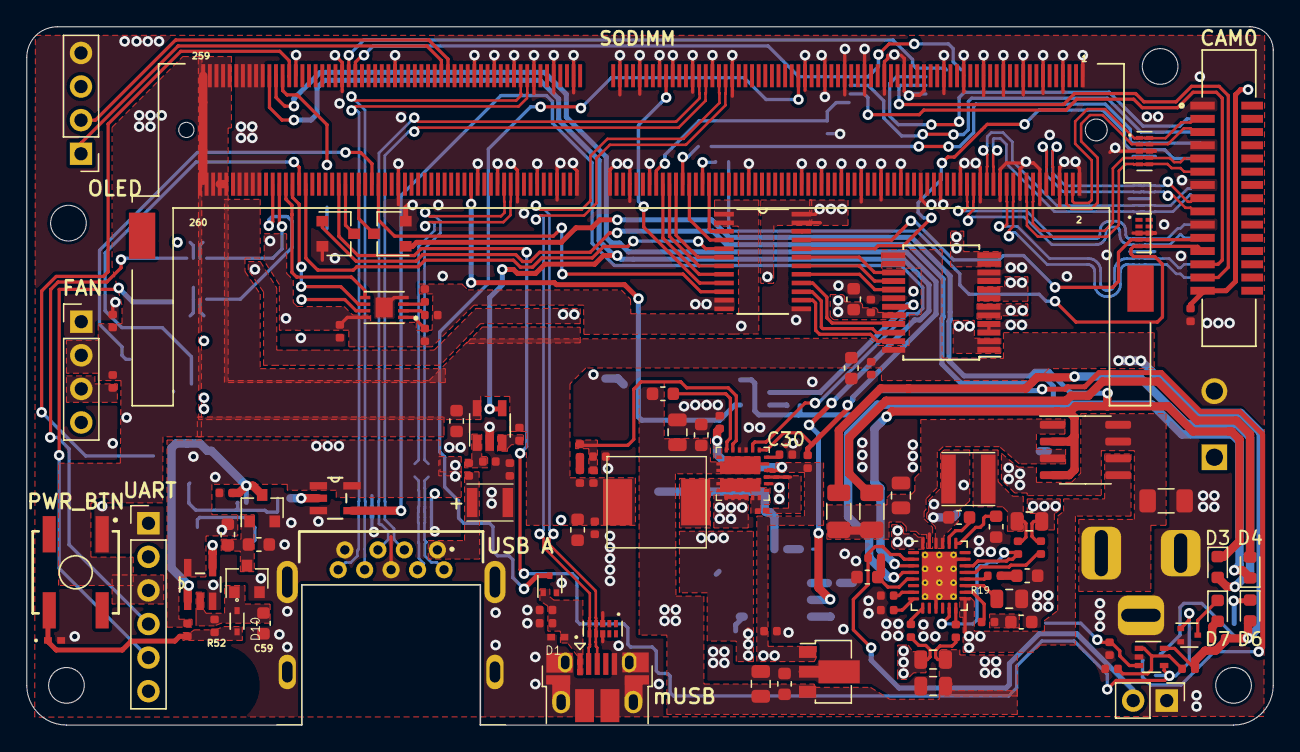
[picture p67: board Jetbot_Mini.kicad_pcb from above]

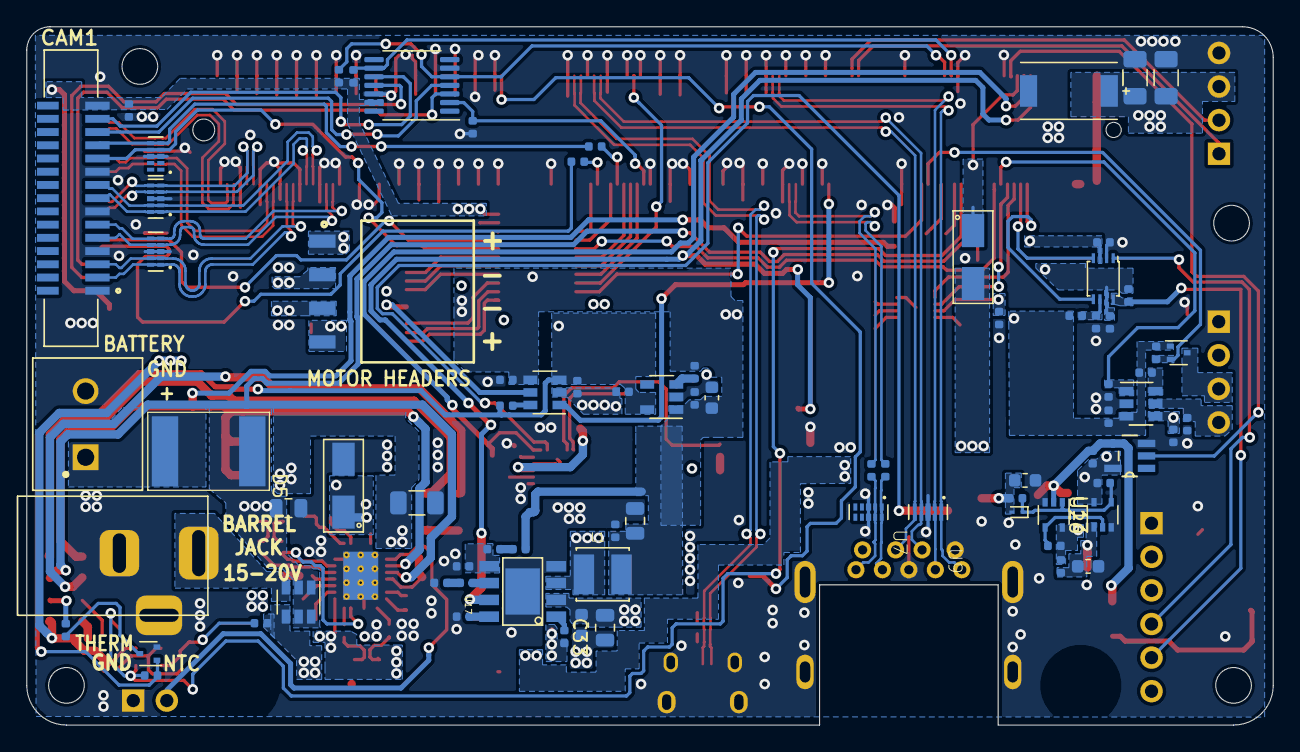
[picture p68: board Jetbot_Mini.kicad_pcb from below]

Board: 4 copper layers, 94.2 x 52.8 mm, 188 parts (79 on the bottom side), 155 nets.

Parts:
C1, C2, C3, C5, C7, C8, C10, C12, C13, C25, C28, C29, C42, C45, C49, C51, C52, C53, C54, C55, C56, C57, C58: 0.1uF; C_0402_1005Metric
C4, C6, C9, C14, C59: 10uF; C_0603_1608Metric
C11: 120uF; 6TPG150MZG
C15: 4.7uF; C_0603_1608Metric
C16: 0.47uF; C_0402_1005Metric
C17, C21, C50: 1uF; C_0603_1608Metric
C18, C27, C34, C35, C44: 0.1uF; C_0603_1608Metric
C19: 0.33uF; C_0805_2012Metric
C20, C23: 10uF; C_1206_3216Metric
C22, C37, C38, C40: 22uF; C_0805_2012Metric
C24: 4.7uF; C_0805_2012Metric
C26, C31: 2.2nF; C_0603_1608Metric
C30, C33: 10nF; C_0402_1005Metric
C32: 6.8nF; C_0402_1005Metric
C36: 2.2nF; C_0201_0603Metric
C39: 47uF; C_0805_2012Metric
C41: Coption; C_0402_1005Metric
C43: 22uF; C_0603_1608Metric
C46: 330uF; 6TPE330MAP
C47, C48: 100uF; C_1206_3216Metric
D1, D9: TPD1E10B06DPYR; DIO_TPD1E05U06DPYR
D2: NSR0620P2T5G; D_SOD-923
D3, D4, D6, D7: LED; LED_0603_1608Metric
D5, D8: B340A-13-F; B340A-13_F
D10: 1N4148WT; SODFL1608X70N
F1: 2920L185DR; 2920_(7351_metric)
H1, H2, H3, H4: MountingHole; MountingHole_2.7mm_M2.5_ISO7380
J1: nvidia_nano_NANO; TE_2309411-5
J2, J3: Conn_01x15_fixed_pin; TE_1-1734248-5
J4: BG300-04-A-L-A; GCT_BG300-04-X-X-A_REVC
J5: Barrel_Jack_Switch; DC_JACK_DC-005-5A-2.5_mirrored
J6: Conn_01x02; PinHeader_1x02_P2.54mm_Vertical
J7: USB_B_Micro_correct_pin; USB_Micro-B_Amphenol_10103594-0001LF_Horizontal
J8: USB3_A; 692121130100_no_edge
J9: Conn_01x04; PinHeader_1x04_P2.54mm_Vertical
J12: 1935161; PHOENIX_1935161
J13: OLED; PinHeader_1x04_P2.54mm_Vertical
J14: Conn_01x06; PinHeader_1x06_P2.54mm_Vertical
L1: 10uH; IND_LQH44PN100MP0L
L2: 10uH; inductor_10uH_2.4A
L3: 4.7uH; MWSA0603-4R7MT
Q1, Q2: DMN26D0UT-7; SOT-523
Q3, Q4: 2N7002; SOT-23
Q5, Q8: DMG1012T; SOT-523
Q6, Q7: 2N7002,215; SC-59
R1, R2, R34, R40, R49, R60, R61: 0; R_0402_1005Metric
R3, R4: 1.6k; R_0402_1005Metric
R5, R6, R9, R10, R11, R12, R15, R16, R17, R18, R22, R26, R31, R39, R42, R46, R48, R51, R53, R55, R56, R57, R59: 10k; R_0402_1005Metric
R7: 1M; R_0402_1005Metric
R8, R21, R50, R54: 100k; R_0402_1005Metric
R13: 2.7M; R_0603_1608Metric
R14, R43: 4.7k; R_0402_1005Metric
R19: 0; R_0805_2012Metric
R20: 470k; R_0402_1005Metric
R23, R24: 1k; R_1206_3216Metric
R25: 2.7k; R_0402_1005Metric
R27, R29: 50; R_0402_1005Metric
R28: 20m; R_0805_2012Metric
R30: 750; R_0402_1005Metric
R32: 6.8k; R_0402_1005Metric
R33: 1.3M; R_0603_1608Metric
R35: 26.1k; R_0402_1005Metric
R36, R37: 402; R_0402_1005Metric
R38: 160m; R_0805_2012Metric
R41: 56k; R_0402_1005Metric
R44: 5.1k; R_0402_1005Metric
R45: 18.7k; R_0402_1005Metric
R47, R58: 150; R_0402_1005Metric
R52: 22k; R_0402_1005Metric
SW1: B3SL-1022P; SW_B3SL-1022P
U1, U2, U5, U7, U9, U25, U28, U30: TPD4E05U06DQAR; TI_TPD4E05U06DQAR
U3: DMP3056LDM-7; SOT-23-6
U4: analog_TC7USB40FT_2; TSSOP-14_4.4x5mm_P0.65mm
U6: TB6612FNG; SSOP-24_5.3x8.2mm_P0.65mm
U8: RT9742CGJ5; TSOT-23-5
U10, U20: PI4ULS5V201TAEX; SOT-23-6
U11, U14: 74LVC1G126W5-7; SOT95P280X145-5N
U12: 74LVC1G07W5-7; SOT95P280X145-5N
U13, U26: MC74VHC1G01DFT1G; SOT-353_SC-70-5
U15: AS78L05; SOT-89-3
U16: MP2619; QFN-28-1EP_4x5mm_P0.5mm_EP2.65x3.65mm_ThermalVias
U17: AP6503; SO-8EP
U18: GS9238
U19: LMV331SE-7; SOT-353_SC-70-5
U21: TXB0102DCU; VSSOP-8_2.4x2.1mm_P0.5mm
U22: AT24C02D-MAHM-T; SON50P200X300X60-9N
U23: 74LVC4245A; SOP65P640X110-24N
U24: TLV70218DBVR_SOT23-5; SOT-23-5
U27: DMP3056LSD-13; SOIC-8_3.9x4.9mm_P1.27mm

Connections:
+1V8: C51.1, C52.1, C53.1, C54.1, C57.1, Q2.1, Q8.1, R9.1, R10.1, R48.1, R49.1, R55.1, R56.1, R57.1, R59.1, U10.3, U20.3, U21.3, U22.8, U23.1, U23.2, U24.5
+3V3: C1.1, C2.1, C3.1, C4.1, C39.1, C42.1, C49.1, C50.1, C55.1, C56.1, J2.15, J3.15, L1.2, R3.1, R4.1, R34.1, R51.1, R54.1, U4.13, U6.20, U10.4, U21.7, U23.23, U23.24, U24.1
+5V: C5.1, C6.1, C9.1, C13.1, C41.1, C43.1, C45.1, C46.1, C47.1, C48.1, C58.1, D6.2, J1.251, J1.252, J1.253, J1.254, J1.255, J1.256, J1.257, J1.258, J1.259, J1.260, J9.2, J13.3, J14.3, L3.2, R6.1, R12.1, R40.1, R43.1, R58.1, U6.13, U6.14, U6.24, U8.5, U19.5, U20.4
+5V_AO: C25.1, C28.1, D8.2, R13.1, R14.1, R15.1, R16.1, R17.1, R18.1, R31.1, U11.5, U12.5, U13.5, U14.1, U14.5, U15.1, U18.7, U18.21, U26.5
+12V: C18.1, C19.1, C22.1, C27.1, C37.1, C38.1, C44.1, R28.1, R29.1, R33.1, R45.1, U3.4, U15.3, U17.2, U18.8, U18.9, U18.22, U18.24
/Camera/CAM0_I2C_SCL: J2.13, U4.3
/Camera/CAM0_I2C_SDA: J2.14, U4.11
/Camera/CAM0_MCLK: J2.12, R1.2, U1.5, U1.6
/Camera/CAM0_MCLK_NANO: J1.116, R1.1
/Camera/CAM0_PWDN_1V8: J1.114, U23.3
/Camera/CAM0_PWDN_3V3: J2.11, U1.4, U1.7, U23.21
/Camera/CAM1_I2C_SCL: J3.13, U4.4
/Camera/CAM1_I2C_SDA: J3.14, U4.10
/Camera/CAM1_MCLK: J3.12, R2.2, U28.5, U28.6
/Camera/CAM1_MCLK_NANO: J1.122, R2.1
/Camera/CAM1_PWDN_1V8: J1.120, U23.4
/Camera/CAM1_PWDN_3V3: J3.11, U23.20, U28.4, U28.7
/Camera/CAM_I2C_SCL: J1.213, R3.2, U4.5
/Camera/CAM_I2C_SDA: J1.215, R4.2, U4.9
/Camera/CAM_SEL: J1.130, R5.1, U4.2
/Camera/CSI0_CLK_N: J1.10, J2.8, U30.5, U30.6
/Camera/CSI0_CLK_P: J1.12, J2.9, U30.4, U30.7
/Camera/CSI0_D0_N: J1.4, J2.2, U5.1, U5.10
/Camera/CSI0_D0_P: J1.6, J2.3, U5.2, U5.9
/Camera/CSI0_D1_N: J1.16, J2.5, U5.4, U5.7
/Camera/CSI0_D1_P: J1.18, J2.6, U5.5, U5.6
/Camera/CSI2_CLK_N: J1.28, J3.8, U30.1, U30.10
/Camera/CSI2_CLK_P: J1.30, J3.9, U30.2, U30.9
/Camera/CSI2_D0_N: J1.22, J3.2, U2.1, U2.10
/Camera/CSI2_D0_P: J1.24, J3.3, U2.2, U2.9
/Camera/CSI2_D1_N: J1.34, J3.5, U2.4, U2.7
/Camera/CSI2_D1_P: J1.36, J3.6, U2.5, U2.6
/Fan/FAN_HEADER_PWM: J9.4, R11.1, U20.5
/Fan/FAN_HEADER_TACH: J9.3, Q2.3, R12.2
/Fan/FAN_LVL_OE: R9.2, U20.6
/Fan/FAN_PWM: J1.230, R8.1, U20.1
/Fan/FAN_TACH: J1.208, Q2.2, R10.2
/Motors/LVL_SHIFT_OE: R59.2, U10.6
/Motors/M1+: J4.4, U6.1, U6.2
/Motors/M1-: J4.3, U6.5, U6.6
/Motors/M2+: J4.1, U6.11, U6.12
/Motors/M2-: J4.2, U6.7, U6.8
/Motors/MC_A1: U6.21, U23.16
/Motors/MC_A2: U6.22, U23.15
/Motors/MC_B1: U6.17, U23.17
/Motors/MC_B2: U6.16, U23.18
/Motors/MC_PWM_A: U6.23, U23.14
/Motors/MC_PWM_B: U6.15, U23.19
/Motors/MOTOR_CNTRL_STBY: U6.19, U10.5
/Motors/~MOD_SLEEP: J1.178, U10.1
/Nano_IO/CHARGER_~ACOK: D3.1, Q6.1, U16.3, U27.2, U27.4
/Nano_IO/CHARGER_~CHGOK: D4.1, Q7.1, U16.4
/Nano_IO/EEPROM_A0: R55.2, U22.1
/Nano_IO/EEPROM_A1: R56.2, U22.2
/Nano_IO/EEPROM_A2: R57.2, U22.3
/Nano_IO/EEPROM_WP: R53.1, U22.7
/Nano_IO/I2C0_SCL: J1.185, J13.2
/Nano_IO/I2C0_SDA: J1.187, J13.1
/Nano_IO/I2C2_SCL: J1.232, U22.6
/Nano_IO/I2C2_SDA: J1.234, U22.5
/Nano_IO/LOW_VOLTAGE_WARNING: J1.218, Q5.1, R48.2, U19.4
/Nano_IO/LVL_SHIFT_EN: R49.2, R50.1, U21.6
/Nano_IO/MC_A1_1V8: J1.128, U23.8
/Nano_IO/MC_A2_1V8: J1.127, U23.9
/Nano_IO/MC_B1_1V8: J1.126, U23.7
/Nano_IO/MC_B2_1V8: J1.124, U23.6
/Nano_IO/MC_PWM_A_1V8: J1.206, U23.10
/Nano_IO/MC_PWM_B_1V8: J1.228, U23.5
/Nano_IO/NANO_CHARGER_~ACOK: J1.212, Q6.3
/Nano_IO/NANO_CHARGER_~CHGOK: J1.216, Q7.3
/Nano_IO/PMIC_BBAT: D8.1, J1.235
/Nano_IO/SHUTDOWN_REQ: J1.233, U12.2
/Nano_IO/UART_DEBUG_RX_1V8: J1.238, U21.5
/Nano_IO/UART_DEBUG_RX_3V3: J14.5, R54.2, U21.8
/Nano_IO/UART_DEBUG_TX_1V8: J1.236, U21.4
/Nano_IO/UART_DEBUG_TX_3V3: J14.4, U21.1
/Nano_IO/VBUS_DET: J1.87, Q1.3
/Power_1/BARREL_JACK_VIN: C20.1, C23.1, J5.1, U3.3, U16.28, U27.7, U27.8
/Power_1/BATTERY_OUTPUT: C40.1, F1.2, R37.1, R38.1, U3.1, U3.2, U3.5, U3.6
/Power_1/Battery_PWR: F1.1, J12.1
/Power_1/CHARGER_BATT: R37.2, U16.19
/Power_1/CHARGER_BST: C35.2, U16.24
/Power_1/CHARGER_CELLS: R19.1, U16.17
/Power_1/CHARGER_COMPI: R30.1, U16.18
/Power_1/CHARGER_COMPV: R25.1, U16.16
/Power_1/CHARGER_CSP: R36.2, U16.13, U16.20
/Power_1/CHARGER_EN: R26.1, U16.7
/Power_1/CHARGER_NTC: J6.2, R21.2, U16.2
/Power_1/CHARGER_PIN: C24.1, R23.2, R24.2, U16.27, U27.1, U27.3
/Power_1/CHARGER_RG1: R27.2, U16.9
/Power_1/CHARGER_RG2: R29.2, U16.14
/Power_1/CHARGER_SHDN: R22.1, U16.8
/Power_1/CHARGER_SW1: C35.1, D5.1, L2.1, U16.25, U16.26
/Power_1/CHARGER_TMR: C34.1, U16.23
/Power_1/CHARGER_VCC: R27.1, R28.2, U16.15, U27.5, U27.6
/Power_1/CHARGER_VREF33: C21.1, R21.1, U16.5
/Power_1/COMPI_CAP: C31.2, R30.2
/Power_1/COMPV_CAP: C26.2, R25.2
/Power_1/IND_SW_OUT: L2.2, R36.1, R38.2
/Power_1/RES_ACOK: D3.2, R23.1
/Power_1/RES_CHGOK: D4.2, R24.1
/Power_2/1V8_REG_EN: R51.2, U24.3
/Power_2/COMPARATOR_V+: R43.2, R44.1, U19.1
/Power_2/COMPARATOR_V-: R45.2, R46.2, U19.3
/Power_2/FET_SOURCE_LV: D7.1, Q5.3
/Power_2/FET_SOURCE_PWR: Q8.3, R47.2
/Power_2/LED_CATHODE_LV: D7.2, R58.2
/Power_2/LED_CATHODE_PWR: D6.1, R47.1
/Power_3/3.3V_BUCK_PWR_EN: J1.239, U8.4, U17.7
/Power_3/3V3_BUCK_BST: C33.1, U17.1
/Power_3/3V3_BUCK_COMP: C32.1, U17.6
/Power_3/3V3_BUCK_FB: R35.2, R39.1, U17.5
/Power_3/3V3_BUCK_SS: C29.1, U17.8
/Power_3/3V3_BUCK_SW: C33.2, L1.1, U17.3
/Power_3/5V_BUCK_BOOT: C36.1, U18.20
/Power_3/5V_BUCK_FB: C41.2, R41.2, R42.1, U18.5
/Power_3/5V_BUCK_LX: C36.2, L3.1, U18.10, U18.11, U18.16, U18.17, U18.18, U18.25
/Power_3/5V_BUCK_PWR_EN: U14.4, U18.2
/Power_3/5V_BUCK_SS: C30.1, U18.23
/Power_3/5V_BUCK_TON: R33.2, U18.6
/Power_3/PGOOD: J1.237, R31.2, U18.1
/Power_Logic/10s_THRESHOLD: C14.1, Q3.3, Q4.1, R13.2
/Power_Logic/BTN_OUT: D9.1, D10.2, R15.2, R52.1, SW1.2
/Power_Logic/BUTTON_OUTPUT: C59.1, D10.1, Q3.1, R52.2, U11.2
/Power_Logic/PWR_CNTRL_BEFORE_BUFFER: C17.1, D2.2, R20.1, U14.2
/Power_Logic/RESET_FB: D2.1, R18.2, R20.2, U13.1, U26.4
/Power_Logic/SET: C15.1, R14.2, U11.4, U26.1
/Power_Logic/SET_FB: R17.2, U13.4, U26.2
/USB/Nano_SS_TX_C+: C8.1, J1.168
/USB/Nano_SS_TX_C-: C7.1, J1.166
/USB/SS_RX+: J1.163, J8.6, U9.2, U9.9
/USB/SS_RX-: J1.161, J8.5, U9.1, U9.10
/USB/SS_TX_C+: C8.2, J8.9, U7.2, U7.9
/USB/SS_TX_C-: C7.2, J8.8, U7.1, U7.10
/USB/USB0+: J1.111, J7.3, U25.4, U25.7
/USB/USB0-: J1.109, J7.2, U25.5, U25.6
/USB/USB1+: J1.117, J8.3, U9.4, U9.7
/USB/USB1-: J1.115, J8.2, U9.5, U9.6
/USB/USB_SWITCH_FLG: R6.2, U8.3
/USB/USB_SWITCH_OUTPUT: C12.1, R60.2, U8.1
/USB/uVBUS: C10.1, D1.1, J7.1, Q1.1, R7.1
GND: C1.2, C2.2, C3.2, C4.2, C5.2, C6.2, C9.2, C10.2, C11.2, C12.2, C13.2, C14.2, C15.2, C16.2, C17.2, C18.2, C19.2, C20.2, C21.2, C22.2, C23.2, C24.2, C25.2, C26.1, C27.2, C28.2, C29.2, C30.2, C31.1, C34.2, C37.2, C38.2, C39.2, C40.2, C42.2, C43.2, C44.2, C45.2, C46.2, C47.2, C48.2, C49.2, C50.2, C51.2, C52.2, C53.2, C54.2, C55.2, C56.2, C57.2, C58.2, C59.2, D1.2, D5.2, D9.2, J1.1, J1.2, J1.7, J1.8, J1.13, J1.14, J1.19, J1.20, J1.25, J1.26, J1.31, J1.32, J1.37, J1.38, J1.43, J1.44, J1.49, J1.50, J1.55, J1.56, J1.61, J1.62, J1.67, J1.68, J1.73, J1.74, J1.79, J1.80, J1.85, J1.86, J1.102, J1.107, J1.113, J1.119, J1.125, J1.129, J1.132, J1.135, J1.138, J1.141, J1.144, J1.146, J1.147, J1.152, J1.153, J1.158, J1.159, J1.164, J1.165, J1.170, J1.171, J1.176, J1.177, J1.200, J1.201, J1.217, J1.231, J1.241, J1.242, J1.243, J1.244, J1.245, J1.246, J1.247, J1.248, J1.249, J1.250, J2.1, J2.4, J2.7, J2.10, J3.1, J3.4, J3.7, J3.10, J5.2, J5.3, J6.1, J7.5, J7.6, J8.4, J8.7, J8.10, J9.1, J12.2, J13.4, J14.1, Q1.2, Q3.2, Q4.2, Q5.2, Q6.2, Q7.2, Q8.2, R5.2, R7.2, R8.2, R11.2, R19.2, R22.2, R26.2, R32.2, R39.2, R42.2, R44.2, R46.1, R50.2, R53.2, R61.1, R61.2, SW1.1, U1.3, U1.8, U2.3, U2.8, U4.6, U4.12, U5.3, U5.8, U6.3, U6.4, U6.9, U6.10, U6.18, U7.3, U7.8, U8.2, U9.3, U9.8, U10.2, U11.3, U12.3, U13.3, U14.3, U15.2, U16.11, U16.21, U16.29, U17.4, U17.9, U18.3, U18.4, U18.12, U18.13, U18.14, U18.15, U18.19, U19.2, U20.2, U21.2, U22.4, U22.9, U23.11, U23.12, U23.13, U23.22, U24.2, U25.3, U25.8, U26.3, U28.3, U28.8, U30.3, U30.8
LATCH_RESET: C16.1, Q4.3, R16.2, U11.1, U12.4, U13.2
unnamed: C32.2, R32.1
unnamed: R34.2, R35.1
unnamed: R40.2, R41.1
unnamed: U1.1, U1.10
unnamed: U1.2, U1.9
unnamed: U7.4, U7.7
unnamed: U7.5, U7.6
unnamed: U25.1, U25.10
unnamed: U25.2, U25.9
unnamed: U28.1, U28.10
unnamed: U28.2, U28.9
VBUS: C11.1, J8.1, R60.1

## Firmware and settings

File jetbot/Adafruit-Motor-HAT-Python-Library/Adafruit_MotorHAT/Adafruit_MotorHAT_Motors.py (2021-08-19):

# Python library for interfacing with the Adafruit Motor HAT for Raspberry Pi to control DC motors with speed control
# and Stepper motors with single, double, interleave and microstepping.

# Designed specifically to work with the Adafruit Motor Hat

# ----> https://www.adafruit.com/product/2348

# Adafruit invests time and resources providing this open source code, please support Adafruit and open-source
# hardware by purchasing products from Adafruit!

# Written by Limor Fried for Adafruit Industries. MIT license. 

# Modified by Joshua Yoon, NVIDIA Corporation & Affiliates, to work with GPIO instead of I2C

import time
import math
import Jetson.GPIO as GPIO

#from Adafruit_MotorHAT.Adafruit_PWM_Servo_Driver import PWM


# class Adafruit_StepperMotor:
#     MICROSTEPS = 8
#     MICROSTEP_CURVE = [0, 50, 98, 142, 180, 212, 236, 250, 255]

    #MICROSTEPS = 16
    # a sinusoidal curve NOT LINEAR!
    #MICROSTEP_CURVE = [0, 25, 50, 74, 98, 120, 141, 162, 180, 197, 212, 225, 236, 244, 250, 253, 255]

    # def __init__(self, controller, num, steps=200):
    #     self.MC = controller
    #     self.revsteps = steps
    #     self.motornum = num
    #     self.sec_per_step = 0.1
    #     self.steppingcounter = 0
    #     self.currentstep = 0

    #     num -= 1

    #     if (num == 0):
    #         self.PWMA = 8
    #         self.AIN2 = 9
    #         self.AIN1 = 10
    #         self.PWMB = 13
    #         self.BIN2 = 12
    #         self.BIN1 = 11
    #     elif (num == 1):
    #         self.PWMA = 2
    #         self.AIN2 = 3
    #         self.AIN1 = 4
    #         self.PWMB = 7
    #         self.BIN2 = 6
    #         self.BIN1 = 5
    #     else:
    #         raise NameError('MotorHAT Stepper must be between 1 and 2 inclusive')

    # def setSpeed(self, rpm):
    #     self.sec_per_step = 60.0 / (self.revsteps * rpm)
    #     self.steppingcounter = 0

    # def oneStep(self, dir, style):
    #     pwm_a = pwm_b = 255

    #     # first determine what sort of stepping procedure we're up to
    #     if (style == Adafruit_MotorHAT.SINGLE):
    #         if ((self.currentstep//(self.MICROSTEPS//2)) % 2):
    #             # we're at an odd step, weird
    #             if (dir == Adafruit_MotorHAT.FORWARD):
    #                 self.currentstep += self.MICROSTEPS//2
    #             else:
    #                 self.currentstep -= self.MICROSTEPS//2
    #         else:
    #             # go to next even step
    #             if (dir == Adafruit_MotorHAT.FORWARD):
    #                 self.currentstep += self.MICROSTEPS
    #             else:
    #                 self.currentstep -= self.MICROSTEPS
    #     if (style == Adafruit_MotorHAT.DOUBLE):
    #         if not (self.currentstep//(self.MICROSTEPS//2) % 2):
    #             # we're at an even step, weird
    #             if (dir == Adafruit_MotorHAT.FORWARD):
    #                 self.currentstep += self.MICROSTEPS//2
    #             else:
    #                 self.currentstep -= self.MICROSTEPS//2
    #         else:
    #             # go to next odd step
    #             if (dir == Adafruit_MotorHAT.FORWARD):
    #                 self.currentstep += self.MICROSTEPS
    #             else:
    #                 self.currentstep -= self.MICROSTEPS
    #     if (style == Adafruit_MotorHAT.INTERLEAVE):
    #         if (dir == Adafruit_MotorHAT.FORWARD):
    #             self.currentstep += self.MICROSTEPS//2
    #         else:
    #             self.currentstep -= self.MICROSTEPS//2

    #     if (style == Adafruit_MotorHAT.MICROSTEP):
    #         if (dir == Adafruit_MotorHAT.FORWARD):
    #             self.currentstep += 1
    #         else:
    #             self.currentstep -= 1

    #             # go to next 'step' and wrap around
    #             self.currentstep += self.MICROSTEPS * 4
    #             self.currentstep %= self.MICROSTEPS * 4

    #         pwm_a = pwm_b = 0
    #         if (self.currentstep >= 0) and (self.currentstep < self.MICROSTEPS):
    #             pwm_a = self.MICROSTEP_CURVE[self.MICROSTEPS - self.currentstep]
    #             pwm_b = self.MICROSTEP_CURVE[self.currentstep]
    #         elif (self.currentstep >= self.MICROSTEPS) and (self.currentstep < self.MICROSTEPS*2):
    #             pwm_a = self.MICROSTEP_CURVE[self.currentstep - self.MICROSTEPS]
    #             pwm_b = self.MICROSTEP_CURVE[self.MICROSTEPS*2 - self.currentstep]
    #         elif (self.currentstep >= self.MICROSTEPS*2) and (self.currentstep < self.MICROSTEPS*3):
    #             pwm_a = self.MICROSTEP_CURVE[self.MICROSTEPS*3 - self.currentstep]
    #             pwm_b = self.MICROSTEP_CURVE[self.currentstep - self.MICROSTEPS*2]
    #         elif (self.currentstep >= self.MICROSTEPS*3) and (self.currentstep < self.MICROSTEPS*4):
    #             pwm_a = self.MICROSTEP_CURVE[self.currentstep - self.MICROSTEPS*3]
    #             pwm_b = self.MICROSTEP_CURVE[self.MICROSTEPS*4 - self.currentstep]


    #     # go to next 'step' and wrap around
    #     self.currentstep += self.MICROSTEPS * 4
    #     self.currentstep %= self.MICROSTEPS * 4

    #     # only really used for microstepping, otherwise always on!
    #     self.MC._pwm.setPWM(self.PWMA, 0, pwm_a*16)
    #     self.MC._pwm.setPWM(self.PWMB, 0, pwm_b*16)

    #     # set up coil energizing!
    #     coils = [0, 0, 0, 0]

    #     if (style == Adafruit_MotorHAT.MICROSTEP):
    #         if (self.currentstep >= 0) and (self.currentstep < self.MICROSTEPS):
    #             coils = [1, 1, 0, 0]
    #         elif (self.currentstep >= self.MICROSTEPS) and (self.currentstep < self.MICROSTEPS*2):
    #             coils = [0, 1, 1, 0]
    #         elif (self.currentstep >= self.MICROSTEPS*2) and (self.currentstep < self.MICROSTEPS*3):
    #             coils = [0, 0, 1, 1]
    #         elif (self.currentstep >= self.MICROSTEPS*3) and (self.currentstep < self.MICROSTEPS*4):
    #             coils = [1, 0, 0, 1]
    #     else:
    #         step2coils = [     [1, 0, 0, 0],
    #             [1, 1, 0, 0],
    #             [0, 1, 0, 0],
    #             [0, 1, 1, 0],
    #             [0, 0, 1, 0],
    #             [0, 0, 1, 1],
    #             [0, 0, 0, 1],
    #             [1, 0, 0, 1] ]
    #         coils = step2coils[self.currentstep//(self.MICROSTEPS//2)]

    #     #print "coils state = " + str(coils)
    #     self.MC.setPin(self.AIN2, coils[0])
    #     self.MC.setPin(self.BIN1, coils[1])
    #     self.MC.setPin(self.AIN1, coils[2])
    #     self.MC.setPin(self.BIN2, coils[3])

    #     return self.currentstep

    # def step(self, steps, direction, stepstyle):
    #     s_per_s = self.sec_per_step
    #     lateststep = 0

    #     if (stepstyle == Adafruit_MotorHAT.INTERLEAVE):
    #         s_per_s = s_per_s / 2.0
    #     if (stepstyle == Adafruit_MotorHAT.MICROSTEP):
    #         s_per_s /= self.MICROSTEPS
    #         steps *= self.MICROSTEPS
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

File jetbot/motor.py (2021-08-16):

# Copyright (c) 2019-2021, NVIDIA CORPORATION. All rights reserved.

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
# The above copyright notice and this permission notice shall be included in all copies or substantial portions of the Software.

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
# Modified by Joshua Yoon to work with GPIO instead of I2C.

import atexit
from Adafruit_MotorHAT import Adafruit_MotorHAT
import traitlets
from traitlets.config.configurable import Configurable
import Jetson.GPIO as GPIO

class Motor(Configurable):

    value = traitlets.Float()
     
    # config
    alpha = traitlets.Float(default_value=1.0).tag(config=True)
    beta = traitlets.Float(default_value=0.0).tag(config=True)

    def __init__(self, driver, channel, *args, **kwargs):
        super(Motor, self).__init__(*args, **kwargs)  # initializes traitlets
 
        self._driver = driver
        self._motor = self._driver.getMotor(channel)
        # if(channel == 1):
        #     self._ina = 1
        #     self._inb = 0
        # else:
        #     self._ina = 2
        #     self._inb = 3
        atexit.register(self._release)
        
    @traitlets.observe('value')
    def _observe_value(self, change):
        self._write_value(change['new'])

    def _write_value(self, value):
        """Sets motor value between [-1, 1]"""
        mapped_value = int(255.0 * (self.alpha * value + self.beta))
        speed = min(max(abs(mapped_value), 0), 255)
        self._motor.setSpeed(speed)
        
        if mapped_value < 0:
            self._motor.run(Adafruit_MotorHAT.FORWARD)
            # The two lines below are required for the Waveshare JetBot Board only
            # self._driver._pwm.setPWM(self._ina,0,0)
            # self._driver._pwm.setPWM(self._inb,0,speed*16)
        else:
            self._motor.run(Adafruit_MotorHAT.BACKWARD)
            # The two lines below are required for the Waveshare JetBot Board only
            # self._driver._pwm.setPWM(self._ina,0,speed*16)
            # self._driver._pwm.setPWM(self._inb,0,0)

    def _release(self):
        """Stops motor by releasing control"""
        self._motor.run(Adafruit_MotorHAT.RELEASE)
        # The two lines below are required for the Waveshare JetBot Board only
        # self._driver._pwm.setPWM(self._ina,0,0)
        # self._driver._pwm.setPWM(self._inb,0,0)

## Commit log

2021-07-23 Add files via upload
    Added A01 Rev3 schematic as test file.
2021-08-03 Added A00 Design Files
    Did not include any 3D models or footprints
    [Camera.sch, Fan.sch, Jetbot Mini.kicad_pcb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]
2021-08-11 Add files via upload
    Uploading some more renderings of Jetbot Mini with shorter battery wire
2021-08-11 Add files via upload
    Uploading more renderings of Jetbot Mini with shorter battery cable
